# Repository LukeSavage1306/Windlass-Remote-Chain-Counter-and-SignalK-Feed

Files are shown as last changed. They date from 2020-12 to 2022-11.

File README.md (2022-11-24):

# Windlass Remote Control with Chain Counter and Signalk Feed

NOTE: As at mid November 2022 the code, pcb link, images etc are the latest version as described below, but I have yet to update the purchasing links  Should be done in next week or so.

Credit for the original version of this app goes to AK-Hombergers.

The current version:

* Is based on a Wemos D1 Mini (ESP8266) reading pulses from a conventional windlass chain sensor with WiFi access to effect control either directly in AP mode or via the boats main wifi in station mode.
* In AP mode uses mDNS for easy access via a named URL rather than remembering IP addresses
* Provides a wireless remote windlass control from any phone/tablet with wifi capability giving up/down/stop/chain-length-counter/counter-reset functionality and the ability to enter a preset scope to which the windlass will automatically raise/lower the chain.
* Provides chain-length to SignalK via a UDP connection
* Works with 12 volt systems - just requires a single transient suppressor diode to be changed for 24v 
* Will also track chain-length when the windlass is operated by existing controls or when allowed to "free fall"
* LED ON indicates that the board should be operating the windlass.  Off indicates board is in standby
* Stores current chain length in nonvolatile memory so that length is stored on switch off and restored after powering back up.
* Demo mode to check correct operation without need for a gypsy sensor present.
* Detects windlass operation from other existing controls and counts chain for up/down/free fall 

Includes various safety features:

- Safety interlock so that Up/Down will not work if another (existing) control is already operating the windlass.
- Safety stop to stop "anchor up" a preset number of gypsy revolutions before reaching zero (can be changed in code with SAFETY_STOP).
- Safety stop if maximum chain length is reached (can be changed with MAX_CHAIN_LENGTH)
- Safety watchdog timer to stop power after predetermined period of inactivity of client (e.g. due to loss of wifi connection).
- Safety watchdog timer to detect blocked chain. Windlass stops if no events are detected within predetermined period of activity after up/down command.

To implement you need to
* Build and install the windlass control board - PCB design available from the link below
* Configure the code (in Arduino)
   - WLAN type setting WiFiMode_AP_STA to "0" (stand alone access point) or "1" (Client with DHCP for SignalK feed).  Note code assumes SignalK server is at 10.10.10.1.  Configure to suit your set up.  More detail on this below.
   - Configure your wifi SSID and password
   - Calibrate for your sensor (e.g. 0.35 meter per revolution of the gypsy) and the maximum chain length
   - Flash the code to the ESP8266

If working as a standalone Access Point, connect the phone/tablet to the defined network (default SSID is "windlass", password "windlass" - can be changed at lines 23 and 24)  and browse to "windlass.local"  (can be changed at line 195)
If working as WLAN client, browsing to "windlass.local" should still work - although I haven't tested it.  If not determine the DHCP IP address using the Arduino Serial Monitor (or other IDE) and start your browser with that IP address.

This should give you a screen as per below on your phone/tablet.  A flashing red dot in the title bar indicates connection established with the Wemos.

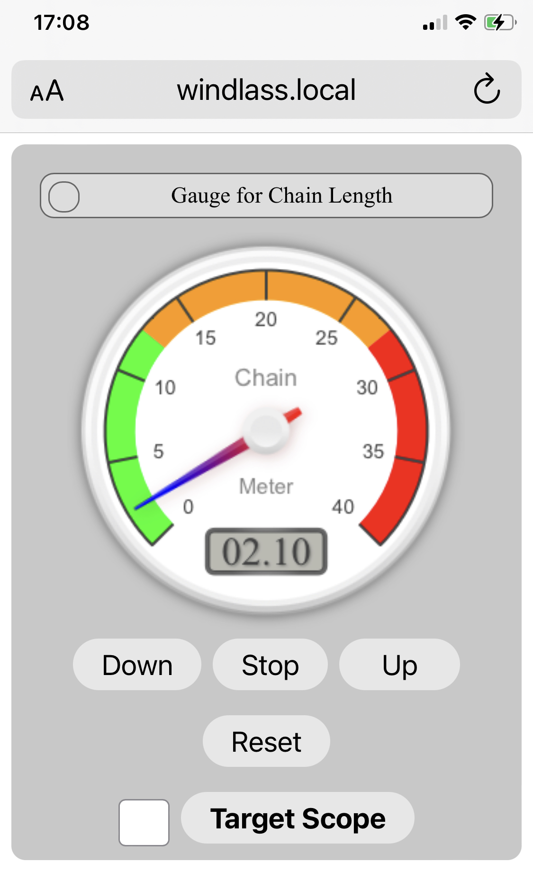
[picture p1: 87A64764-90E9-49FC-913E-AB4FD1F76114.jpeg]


To control the anchor chain relay just press:
- "Down" for anchor down
- "Up" for anchor up
- "Stop" for Stop
- "Reset" to reset the chain counter to zero
- Or enter the desired scope and hit "Target Scope" to pay out/pull in to the set length

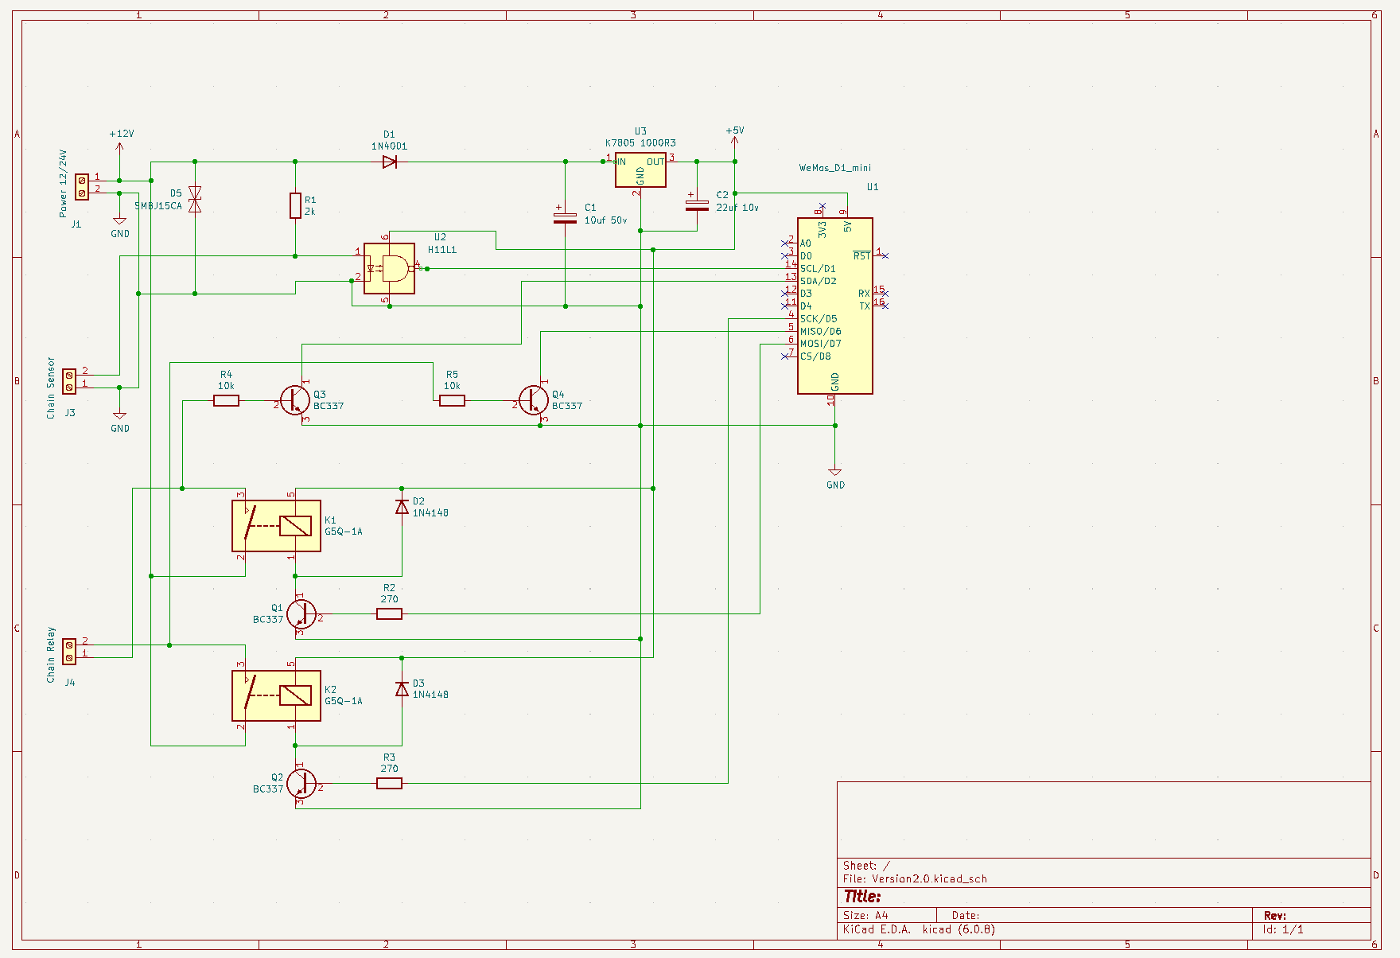
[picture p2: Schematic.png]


A [pcb layout](https://github.com/LukeSavage1306/Windlass-Remote-Chain-Counter-and-SignalK-Feed/blob/main/24vD1MiniWindlassControlAndChainCounter.kicad_pcb) is available in the main folder. 

You can order a PCB from Aisler.net:  https://aisler.net/p/LRMWVSQR

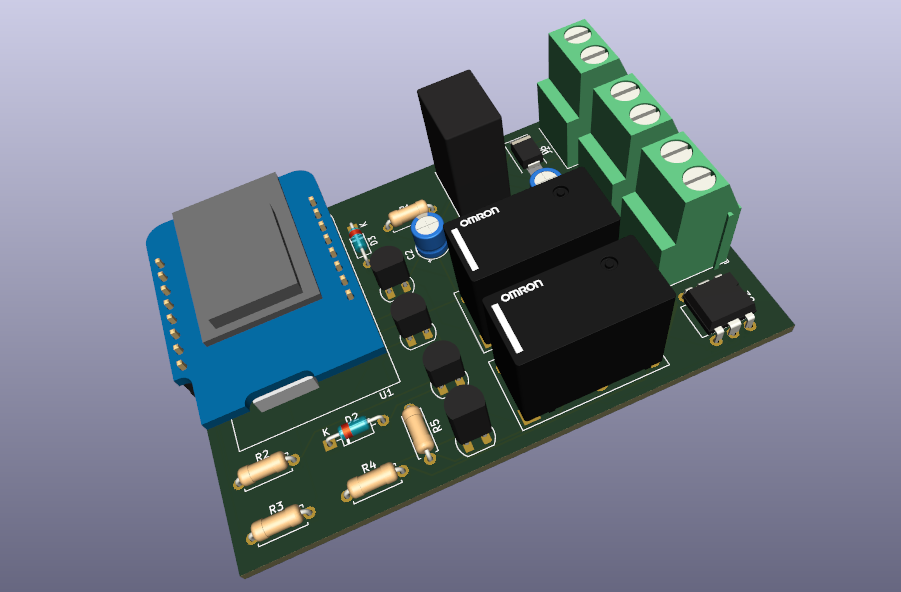
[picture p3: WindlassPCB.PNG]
Board


## Parts:

Parts list currently points to largely German suppliers but are generally widely available with the exception of the PCB. If you want to source these elsewhere I can provide the detailed KiCad files. 

- Board [Link](https://aisler.net/p/ESKPZAUS)
- U1 D1 Mini [Link](https://www.reichelt.de/de/en/d1-mini-esp8266-v3-0-d1-mini-p253978.html?&nbc=1)
- U3 K7805 1000R3L [Link](https://uk.rs-online.com/web/p/switching-regulators/1934015/)
- C1 10uF 50v can electrolytic (can be reduced to 25v if running on a 12V system)
- C2 22uF 15v can electrolytic 
- R1 Resistor 5 KOhm (if using 12v you can reduce this to 2.2 Kohm to ensure accurate counting at low battery voltage) [Link](https://www.reichelt.de/de/en/carbon-film-resistor-1-4-w-5-1-0-kilo-ohms-1-4w-1-0k-p1315.html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)
- R2, R3 Resistor 270 Ohm (*2) [Link](https://www.reichelt.de/de/en/carbon-film-resistor-1-4-w-5-270-ohm-1-4w-270-p1390.html?&nbc=1)
- R4, R5 Resistor 10 KOhm (*2) [Link](https://www.reichelt.de/de/en/carbon-film-resistor-1-4w-5-10-kilo-ohms-1-4w-10k-p1338.html?&nbc=1)
- Q1, Q2, Q3, Q4 Transistor BC337 (*4) [Link](https://www.reichelt.de/de/en/transistor-to-92-bl-npn-45v-800ma-bc-337-25-dio-p219125.html?&nbc=1)
- D2, D3 Diode 1N4148 (*2) [Link](https://www.reichelt.de/schalt-diode-100-v-150-ma-do-35-1n-4148-p1730.html?search=1n4148)
- D1 Diode 1N4001 [Link](https://www.reichelt.de/de/en/rectifier-diode-do41-50-v-1-a-1n-4001-p1723.html?&nbc=1)
- U2 H11-L1 [Link](https://www.reichelt.de/optokoppler-1-mbit-s-dil-6-h11l1m-p219351.html?search=H11-l1)
- K1, K2 Relay (*2) [Link](https://www.reichelt.de/de/en/miniature-power-relay-g5q-1-no-5-v-dc-5-a-g5q-1a-eu-5dc-p258331.html?&nbc=1)
- J1, J3, J4 Connector 2-pin (*3) [Link](https://www.reichelt.de/de/en/2-pin-terminal-strip-spacing-5-08-akl-101-02-p36605.html?&nbc=1)

The current design should work for a Quick or Lofrans anchor chain relay and chain sensor (which looks like a simple reed relay triggerd from a magnet). Connection details  for a Quick windlass/counter can be found here: https://www.quickitaly.com/resources/downloads_qne-prod/1/CHC1203_IT-EN-FR_REV001A.pdf

The board requires connection to your windlass power supply (12v - for 24v change the transient suppressor diode D4 for circa 29v equivalent - no other configuration necessary), connection to your windlass sensor (polarity of connection does not matter) and connection of the Up and Down relay feeds to the existing Up and Down terminals on the main windlass relay (note: the switching terminals that connect to any existing switch controls - NOT the motor output terminals).

To access via the main boat wifi or to send data to SignalK you need to set up in Station mode.  To do that set WiFIMode_AP_STA to 1 at line 21 and define the main boat wifi SSID and Password at lines 23 and 24.   Define the signalk server IP and port at lines 25 and 26.  In Signalk you muse also define a UDP connection.  Go to Server, Connections and define a new connection as per the picture below.  Match the port number to the number you used in the .ino code (default is 4210).  Once configured ChainLength should appear as a data item within the Data Browser.

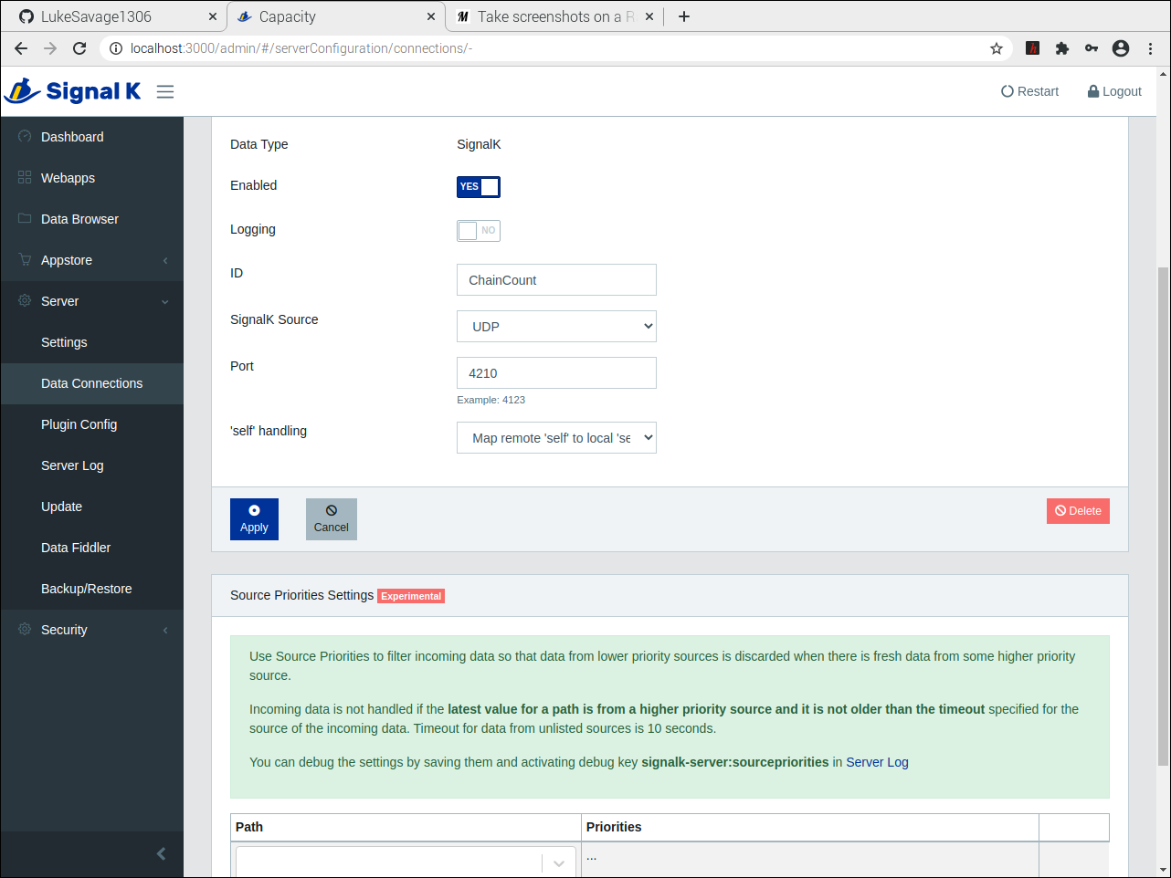
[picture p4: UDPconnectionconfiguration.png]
UDP connection


The gauge display can be changed to mirror your particular chain length in index_html.h   The range is set at lines 133/134 and the coloured zones at line 144

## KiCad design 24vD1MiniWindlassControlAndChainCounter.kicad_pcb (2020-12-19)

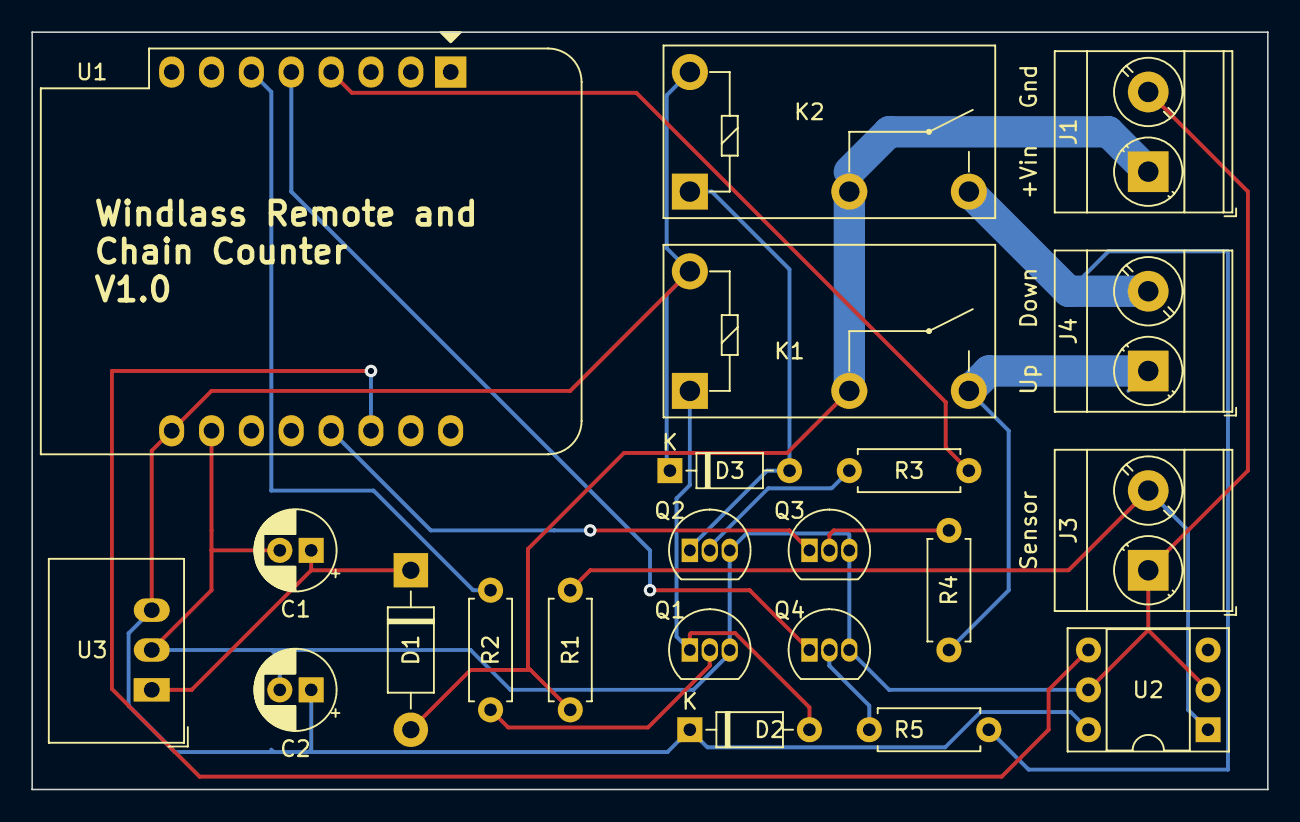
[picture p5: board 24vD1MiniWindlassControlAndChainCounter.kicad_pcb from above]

Board: 2 copper layers, 78.7 x 48.3 mm, 22 parts (0 on the bottom side), 18 nets.

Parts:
C1: 10uF 50V; CP_Radial_D5.0mm_P2.00mm
C2: 22uF10V; CP_Radial_D5.0mm_P2.00mm
D1: 1N4001; D_DO-41_SOD81_P10.16mm_Horizontal
D2, D3: 1N4148; D_DO-35_SOD27_P7.62mm_Horizontal
J1: Power 12/24V; TerminalBlock_Phoenix_MKDS-3-2-5.08_1x02_P5.08mm_Horizontal
J3: Chain Sensor; TerminalBlock_Phoenix_MKDS-3-2-5.08_1x02_P5.08mm_Horizontal
J4: Chain Relay; TerminalBlock_Phoenix_MKDS-3-2-5.08_1x02_P5.08mm_Horizontal
K1, K2: G5Q-1A; Relay_SPST_Omron-G5Q-1A
Q1, Q2, Q3, Q4: BC337; TO-92_Inline
R1: 5k; R_Axial_DIN0207_L6.3mm_D2.5mm_P7.62mm_Horizontal
R2, R3: 270; R_Axial_DIN0207_L6.3mm_D2.5mm_P7.62mm_Horizontal
R4, R5: 10k; R_Axial_DIN0207_L6.3mm_D2.5mm_P7.62mm_Horizontal
U1: WeMos_D1_mini; WEMOS_D1_mini_light
U2: H11L1; DIP-6_W7.62mm_Socket
U3: K7805 1000R3L; Converter_DCDC_RECOM_R-78E-0.5_THT

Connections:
+5V: C2.1, D2.1, D3.1, K1.5, K2.5, U1.9, U2.6, U3.3
+12V: D1.2, J1.1, K1.2, K2.2, R1.1
GND: C1.2, C2.2, J1.2, J3.1, Q1.3, Q2.3, Q3.3, Q4.3, U1.10, U2.2, U2.5, U3.2
unnamed: C1.1, D1.1, U3.1
unnamed: D2.2, K1.1, Q1.1
unnamed: D3.2, K2.1, Q2.1
unnamed: J3.2, R1.2, U2.1
unnamed: J4.1, K1.3, R4.2
unnamed: J4.2, K2.3, R5.2
unnamed: Q1.2, R2.2
unnamed: Q2.2, R3.2
unnamed: Q3.1, U1.13
unnamed: Q3.2, R4.1
unnamed: Q4.1, U1.5
unnamed: Q4.2, R5.1
unnamed: R2.1, U1.6
unnamed: R3.1, U1.4
unnamed: U1.14, U2.4

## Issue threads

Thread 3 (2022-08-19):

Cannot connect to SignalK

MrTom1, 2022-08-19:
I followed exactly your settings to connect to SignalK, however I can not establish any connection. Port settings are same on both sides.
Any advice how to move ahead?

LukeSavage1306, 2022-08-23:
Hi Tom, sorry for slow response.  Have you tried configuring the counter for stand alone use, and then tried connecting directly to its WiFi from your phone?  That way you can make sure that the chip is good and the code is running properly to begin with.   You would then know it is the signalk connection that is playing up rather than a duff chip or bad copy of the code.    Let me know how you get on and we can then work out the next step.

MrTom1, 2022-08-23:
Hi Luke,
Thanks for your reply.
The board is working fine, I can connect to my smartphone and control it from there.
In SignalK I have added the corresponding UDP connection, but no data transfer to there.

LukeSavage1306, 2022-08-23:
So what are the settings you have in the chain counter for connecting to your signal K server?  Do you want to copy and paste those few lines of code?   By the way - I have never done this sort of thing before or since taking Homberger’s counter and making the changes.  I learnt as I went along - largely by trial and error - and that was 2 1/2 years ago.  I only mention that as any help I can give now will also be largely by trial and error!!

MrTom1, 2022-08-23:
So let's try it!
IP address for UDP to SignalK has been adapted (port is 4210, also setup in SignalK according to your manual):
IPAddress ip1(10, 81, 254, 242);           // IP Address to be used for SiganlK so that udp knows where to send messages - amend if yours is different
MMSI adapted:
  char udpmessage[1024];    //Next few lines send metadata to SignalK for chainlength - replace mmsi with your own "self" vessel details
      sprintf(udpmessage, "{\"context\": \"vessels.urn: mrn: imo: mmsi:211695590\",\"updates\": [{\"meta\":[{\"path\": \"navigation.anchor.chainlength\",\"value\": {\"units\": \"m\",\"description\": \"deployed chain length\",\"displayName\": \"Chain Length\",\"shortName\": \"DCL\"}}]}]}");

LukeSavage1306, 2022-08-23:
And line 34 (which you would set to 0 to connect direct) has been reset to 1?

What are you running signalK on?  I used a Raspberry Pi where the default IP for a local host was 10.10.10.1 and that worked fine. I wonder whether in configuring your signalk server as well as changing the IP something else has been changed.

LukeSavage1306, 2022-08-23:
Just re-reading my notes, once connected via the main WiFi (rather than using it standalone) can you access the chain counter from you phone?  But just can’t see the data in signalK?   Or can you not access it from your phone when using it as a client to the main WiFi?

MrTom1, 2022-08-23:
#define WiFiMode_AP_STA 1
IPAddress ip1(10, 81, 254, 242);           // IP Address to be used for SiganlK so that udp knows where to send messages - amend if yours is different

ip1 is the address of the ESP8266 board. This address I also use to run it from my smartphone. Does this address has to be changed?
I changed ip1 to 10.10.10.1 (running on Raspberry Pi) and get the following with the monitor:
WiFi connected
IP address:
10.81.254.242
Now listening at IP 10.81.254.242, UDP port 4210
Metadata sent to SignalKHTTP Server started
{"updates":[{"$source":"Windlass.Control","values":[{"path":"navigation.anchor.chainlength","value":1.650000}]}]}

MrTom1, 2022-08-23:
See above, but still no data for "navigation.anchor.chainlength"

LukeSavage1306, 2022-08-23:
From memory (as I did all of this on another computer at a different location)

The ESP connects to the general boat WiFi router and is allocated an IP address by DHCP.   Your phone, connected to the boat’s WiFi router, then connects to the ESP at the IP allocated via the boat’s router.  It sounds from what you are saying as if that bit is working OK??
Once you are happy that the ESP is accessible via the boat’s WiFi, so we know that it is hooked in, the next thing is then how to get the UDP messages into SignalK.  For that the ESP has to send the messages to the SignalK server running as “local host”.  I think, but can’t remember for sure, that is at 10.10.10.1
I’m afraid I am not going to be back at the location I did this at for a few weeks - and even then I would have to “start again” as, off the top of my head, I can’t even remember how one programmes the ESP from Arduino!!!

LukeSavage1306, 2022-08-23:
Just looking at the code - line 38 is definitely telling the ESP the IP address of SignalK.  So it should be whatever IP your SignalK server is running at, not the IP of the ESP.  Something also makes me think that it sends data when there is an update to the value, not on a regular basis, so if you are not winding up or down it won’t be sending anything.  Not sure my knowledge of the coding is good enough to confirm that from “reading” it rather than trying it!

To help get it working (which took me days of trial and error) I wired up a simple switch to simulate the windlass switch - and I think changed the timeout time so that I could do it slowly

MrTom1, 2022-08-23:
Got it running!
ip1 set to the correct address of the Raspi SignalK Server (10.81.254. ...) and it works fine!

Thanks for your time and advices!
Tom

LukeSavage1306, 2022-08-23:
At line 166 it seems you should see a line on the monitor if the metadata has been correctly sent.  Are you seeing that?

LukeSavage1306, 2022-08-23:
Brilliant.  One thing to check when you install it.  Depending on the rating of your windlass power relay the current draw to operate the relay could be quite high.  Part of the redesign of the circuit board from Homberger’s original design was to upgrade the size of, and shorten the PCB tracks between the onboard relay and the connector.  On mine it seems OK - but you may want to check that the board isn’t getting hot in that area.

Good luck - I hope it makes your anchoring easier.  Where are you based by the way??

Luke

On 23 Aug 2022, at 15:25, MrTom1 ***@***.***> wrote:

Got it running!
ip1 set to the correct address of the Raspi SignalK Server (10.81.254. ...) and it works fine!

Thanks for your time and advices!
Tom

—
Reply to this email directly, view it on GitHub, or unsubscribe.
You are receiving this because you commented.

MrTom1, 2022-08-23:
Good advice to check the current and signal line.

I'm based at Lake of Constance, Germany
Another happy user of the anchoring tool there now ;-)

LukeSavage1306, 2022-08-23:
Great.  If you have any ideas on improvements let me know.  In the meantime I’m going to close the thread.
Regards
Luke

Closed 2022-08-23.

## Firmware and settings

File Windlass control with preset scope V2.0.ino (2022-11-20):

// Anchor Chain Remote Control / Chain Counter with WLAN.
// and Preset Target Scope
// SignalK feed, external control, freefall, LED status
// Version 2.0  07/11/2022

#include<ESP8266WiFi.h>
#include<ESP8266WebServer.h>
#include<EEPROM.h>
#include <WiFiUdp.h>
#include <ESP8266mDNS.h>              // Used to enable web browser to find by URL rather than IP address


#include "index_html.h"              // Webserver script for Gauge/Buttons on phone/tablet

#define ENABLE_DEMO 1                // Set to 1 to enable Demo Mode with up/down counter
#define SAFETY_STOP 2                // Defines safety stop for chain up. Stops defined number of revolutions before reaching zero
#define MAX_CHAIN_LENGTH 39          // Define maximum chain lengthin metres. Relay turns off after the value is reached

// Wifi: Select AP or Client

#define WiFiMode_AP_STA 0             // Defines WiFi Mode 0 -> AP (with IP:192.168.4.1 stand alone and  1 -> Station (client with IP: via DHCP)
                                        // To use both the windlass control and feed SignalK you have to set to 1 as a Station 
const char *ssid = "Windlass";          // Set WLAN name for station connection
const char *password = "Windlass";  // Set password for station connection
IPAddress ip1(10, 10, 10, 1);           // IP Address to be used for SiganlK so that udp knows where to send messages - amend if yours is different
unsigned int outPort = 4210;            // and which port to send to


ESP8266WebServer server(80);                //Define Web Server at port 80 for general connection to central boat wifi


// Chain Counter
 
#define Chain_Calibration_Value 0.35 // Translates counter pulses to metres per revolution - change this to suit your windlass
#define Chain_Counter_Pin D1         // Counter impulse is measured as interrupt on pin D1, GPIO pin 05
unsigned long Last_int_time = 0;     // Time of last interrupt
unsigned long Last_event_time = 0;   // Time of last event for engine watchdog
unsigned long Last_stop_time = 0;    // Time of stop request - used to continue correct counting while windlass slows to a halt
unsigned long Sprint_timer = 0;       // Timer to control serial monitor printing
int ChainCounter = 0;                // Counter for chain events
int Scope = 0;                        // Preset Target Scope
int LastSavedCounter = 0;            // Stores last ChainCounter value to allow storage to nonvolatile storage in case of value changes

// Relay

#define Chain_Up_Pin D7              // GPIO pin 13 for Chain Up Relay       (If using a board other than Wemos D1 mini then check all pins)
#define Chain_Down_Pin D5            // GPIO pin 14 for Chain Down Relay      
#define Chain_Up_Override_Pin D2     // GPIO pin 04 for Chain Up Override     
#define Chain_Down_Override_Pin D6   // GPIO pin 12 for Chain Down Override   
int UpDown = 1;                      // 1 =  Chain down / count up, -1 = Chain up / count backwards
int OnOff = 0;                       // Relay On/Off - Off = 0, On = 1
int Preset = 0;                      // Flag to control logic in reaching preset scope
unsigned long Watchdog_Timer = 0;    // Watchdog timer to stop relay after 1 second of inactivity e.g. connection loss to client


// Chain Event Interrupt
// Enters on falling edge

void IRAM_ATTR handleInterrupt() {    //This section debounces the chain sensor to avoid multipe counts from one switch event
  noInterrupts();

  if (millis() > Last_int_time + 100) {  // Debouncing. No new events for 100 milliseconds - still a fraction of a turn of the windlass

    ChainCounter += UpDown;             //Increment/decrement chain counter based on sign of UpDown

  //This section handles testing against reaching a preset value

    if ((Preset == 1) && (UpDown == 1) && (Scope-(ChainCounter*Chain_Calibration_Value) <= 0 )) {       //Test to see if chain let out to preset scope - and if so....
    OnOff = 0;                                                                                        //Set status to off
    Last_stop_time = millis();                                                                        //Record time (used to allow for deceleration interval of windlass)      
    Preset = 0;                                                                                       //Flag end of preset operation
    digitalWrite(Chain_Up_Pin, LOW );                                                                 //Make sure both relays are off  
    digitalWrite(Chain_Down_Pin, LOW);
  }

  if ((Preset == 1) && (UpDown == -1) && ((ChainCounter*Chain_Calibration_Value)-Scope <= 0 )) {      //Test to see if chain is taken in to preset scope - and if so.....
    OnOff = 0;                                                                                        //Set status to off
    Last_stop_time = millis();                                                                        //Record time (used to allow for deceleration interval of windlass)
    Preset = 0;                                                                                       //Flag end of preset operation
    digitalWrite(Chain_Up_Pin, LOW );                                                                 //Make sure both relays are off
    digitalWrite(Chain_Down_Pin, LOW);
  }

   //This section handles reaching the upper safety stop limit     

  if ( ( (ChainCounter <= SAFETY_STOP) && (UpDown == -1) && (OnOff == 1) )) {    // If safety stop counter reached while chain is going up - 
    digitalWrite(Chain_Up_Pin, LOW );                                             // Turn off both relays
    digitalWrite(Chain_Down_Pin, LOW );
    OnOff = 0;                                                                    // Set the status to off
    Last_stop_time = millis();
    Serial.print("Up safety stop reached - Turning off Up relay and UpDown state is ");
    Serial.println(UpDown);
    }
  
  
  
  if  ( (UpDown == 1) && (abs(ChainCounter) * Chain_Calibration_Value >= MAX_CHAIN_LENGTH) )  {  // Maximum chain length reached - so turn off

    digitalWrite(Chain_Up_Pin, LOW );
    digitalWrite(Chain_Down_Pin, LOW );
    OnOff = 0;
    Serial.print("Maximum chain length reached - Turning off Down relay and UpDown state is ");
    Serial.println(UpDown);

    } 
    Last_event_time = millis();         // Store last event time to detect blocking chain
    }

  
  Last_int_time = millis();             // Store last interrupt time for debouncing
  interrupts();
}

 WiFiUDP Udp;                         // Configure UDP - not sure if these lines are necessary as we are transmitting rather than receiving via UDP
unsigned int localUdpPort = 4210;  // local port to listen on
char incomingPacket[255];  // buffer for incoming packets
char  replyPacket[] = "Hi there! Got the message :-)";  // a reply string to send back


void setup() {
  
  // LED indicator
  pinMode(LED_BUILTIN,OUTPUT); //Define LED pin as output
  digitalWrite(LED_BUILTIN,HIGH); //and turn it off
  
  int wifi_retry = 0;

  // Relay output
  pinMode(Chain_Up_Pin, OUTPUT);            // Sets pin as output
  pinMode(Chain_Down_Pin, OUTPUT);          // Sets pin as output
  digitalWrite(Chain_Up_Pin, LOW );         // and relay off
  digitalWrite(Chain_Down_Pin, LOW );       // and relay off
  
  //Over Ride input
  pinMode(Chain_Down_Override_Pin, INPUT_PULLUP);  // Sets pin as input pulled high 
  pinMode(Chain_Up_Override_Pin, INPUT_PULLUP);    // Sets pin as input pulled high

  // Init Chain Count measure with interrupt
  pinMode(Chain_Counter_Pin, INPUT_PULLUP); // Sets pin as input pulled high
  attachInterrupt(digitalPinToInterrupt(Chain_Counter_Pin), handleInterrupt, FALLING); // Attaches pin to interrupt on falling edge

  // Init serial monitor for debugging
  Serial.begin(38400);
  Serial.print("");
  Serial.println("Start");

  EEPROM.begin(16);
  ChainCounter = EEPROM.read(0);
  LastSavedCounter = ChainCounter;                  // Initialise last counter value so that after power off it restarts with the same length

  // Init WLAN AP
  if (WiFiMode_AP_STA == 0) {

    WiFi.mode(WIFI_AP);                              // WiFi Mode Access Point
    delay (100);
    WiFi.softAP(ssid, password); // AP name and password
    Serial.println("Start WLAN AP");
    Serial.print("IP address: ");
    Serial.println(WiFi.softAPIP());



  } else {

    Serial.println("Start WLAN Client DHCP");         // WiFi Mode Client with DHCP
    WiFi.begin(ssid, password);

    while (WiFi.status() != WL_CONNECTED) {           // Check connection
      wifi_retry++;
      delay(500);
      Serial.print(".");
      if (wifi_retry > 10) {
        Serial.println("\nReboot");                   // Reboot after 10 connection tries
        ESP.restart();
      }
    }
  Serial.println("");
  Serial.println("WiFi connected");
  Serial.println("IP address: ");
  Serial.println(WiFi.localIP());
  
  Udp.begin(localUdpPort);
  
  Serial.printf("Now listening at IP %s, UDP port %d\n", WiFi.localIP().toString().c_str(), localUdpPort);
  
      char udpmessage[1024];    //Next few lines send metadata to SignalK for chainlength - replace mmsi with your own "self" vessel details
      sprintf(udpmessage, "{\"context\": \"vessels.urn: mrn: imo: mmsi: 235083375\",\"updates\": [{\"meta\":[{\"path\": \"navigation.anchor.chainlength\",\"value\": {\"units\": \"m\",\"description\": \"deployed chain length\",\"displayName\": \"Chain Length\",\"shortName\": \"DCL\"}}]}]}");
      Udp.beginPacket(ip1, outPort);
      Udp.write(udpmessage);
      Udp.endPacket();
      Serial.printf("Metadata sent to SignalK");
      
}

if (!MDNS.begin("windlass")) {                                                // Start the mDNS responder for windlass.local
    Serial.println("Error setting up MDNS responder!");
  }
  Serial.println("mDNS responder started");


// Handle HTTP request events from phone/tablet

server.on("/", Event_Index);
server.on("/gauge.min.js", Event_js);
server.on("/ADC.txt", Event_ChainCount);
server.on("/up", Event_Up);
server.on("/down", Event_Down);
server.on("/stop", Event_Stop);
server.on("/reset", Event_Reset);
server.on("/preset", Event_Preset);
server.onNotFound(handleNotFound);

server.begin();
Serial.println("HTTP Server started");
}

//HANDLE UP REQUEST
void Event_Up() {    
  if (((OnOff == 0 && digitalRead(Chain_Up_Override_Pin) == HIGH && digitalRead(Chain_Down_Override_Pin) == HIGH)) || (OnOff == 1)) { // Execute only if the app is already on, or if there isn't a manual override present
    server.send(200, "text/plain", "-1000");                                                                                          // Send response "-1000" means no  chainlength
     UpDown = -1;																													// Set chain counter to reduce scope
    Serial.println("Up button pressed - setting UpDown to -1 and Turning on Up relay by setting Chain_Up_Pin to High");				//Debug message
      digitalWrite(Chain_Down_Pin, LOW );                                                                                             //  Make sure down relay is off
      digitalWrite(Chain_Up_Pin, HIGH ); 																							//Then turn up relay on																						
      OnOff = 1;																													//With app on
      Preset = 0;																													//And target preset scope off
       Last_event_time = millis();                                        //Record event time for checking if windlass is jammed
  }
}
//HANDLE DOWN REQUEST
void Event_Down() {  
  if (((OnOff == 0 && digitalRead(Chain_Up_Override_Pin) == HIGH && digitalRead(Chain_Down_Override_Pin) == HIGH)) || (OnOff == 1)) { // Execute only if the app is already on, or if there isn't a manual override present
    server.send(200, "text/plain", "-1000");  // Send response "-1000" means no  chainlength
    UpDown = 1;                                                                                                                       // Set chain counter to increase scope
    Serial.println("Down button pressed - setting UpDown to 1 and Turning on Down relay by setting Chain_Down_Pin to High");          // Debug message
    digitalWrite(Chain_Up_Pin, LOW );                                                                                                 // Make sure up relay is off
    digitalWrite(Chain_Down_Pin, HIGH );                                                                                              // And turn down relay on
    Last_event_time = millis();                                                                                                       // Record event time for checking if windlass is jammed
    OnOff = 1;                                                                                                                        // With app on
    Preset = 0;                                                                                                                       // and preset off 
  Last_stop_time = millis();                                                                                                          // Record event time for checking if windlass is jammed
  }
}
//HANDLE STOP REQUEST
void Event_Stop() {  
  server.send(200, "text/plain", "-1000");  // Send response "-1000" means no  chainlength
  Serial.print("Stop button pressed - setting both Chain Pins to Low, current UpDown state is ");                                     // Debug message
  Serial.println(UpDown);                                                                                                             // Debug message    
  Last_stop_time = millis();
  digitalWrite(Chain_Up_Pin, LOW );                                                       // Make sure both relays are off
  digitalWrite(Chain_Down_Pin, LOW );
  OnOff = 0;                                                                              // With app off
  Preset = 0;                                                                             // And Preset off
}


//HANDLE REQUEST TO RESET COUNTER TO ZERO
void Event_Reset() {        
    ChainCounter = 0;                                             //Reset counter to zero
  server.send(200, "text/plain", "-1000");  // Send response "-1000" means no  chainlength
  Serial.println("Reset gauge to zero");                          //Debug message
}


//HANDLE PRESET SCOPE LENGTH REQUEST
void Event_Preset() {               
  server.send(200, "text/html", indexHTML);                                                                                           // Refresh browser page (ideally don't but can't work out how not to)
  Scope = (server.arg(0)).toInt();                                                                                                    // Take preset scope from input and convert it to an integer     

  Serial.print("Scope has been set to ");                                                                                             // Send length to serial print for debugging
  Serial.println(Scope);

  Preset = 1;                                                                                                                         // Set Flag for preset scope logic
  if (Scope - (ChainCounter*Chain_Calibration_Value) > 0) {                                                                           // Determine if chain needs to go out to reach preset scope
  Serial.println ("Chain needs to go out by ");                                                                                       // Debug message 
  Serial.println (Scope - (ChainCounter*Chain_Calibration_Value));                                                                    // Debug message
  UpDown =1;                                                                                                                          // Set counter for down                                 
  digitalWrite(Chain_Up_Pin, LOW);                                                                                                    //Make sure up relay is off and 
  digitalWrite(Chain_Down_Pin, HIGH);                                                                                                // Turn on down relay
  OnOff = 1;                                                                                                                        // And flag that app is on

  } else {                                                                                                                             //Chain needs to come up to reach preset scope
  Serial.println ("Chain needs to go up by ");
  Serial.println ((ChainCounter*Chain_Calibration_Value)-Scope);
  UpDown = -1;                                                                                                                        //Set counter for up
  digitalWrite(Chain_Down_Pin, LOW);                                                                                                  //Make sure down relay is off and 
  digitalWrite(Chain_Up_Pin, HIGH);                                                                                                   // Turn on up relay
  OnOff = 1;                                                                                                                          // And flag that app is on
  }
  Last_event_time = millis(); 
  Watchdog_Timer = millis();     
}

void Event_Index() {                         // If "http://<ip address>/" requested
  server.send(200, "text/html", indexHTML);  // Send Index Website
}


void Event_js() {                            // If "http://<ip address>/gauge.min.js" requested
  server.send(200, "text/html", gauge);      // Then send gauge.min.js
}
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
void loop() {
  int wifi_retry = 0;
  MDNS.update();                                                    // Check to see if browser is looking for IP address
  server.handleClient();                                           // Handle HTTP requests

  if ( ( millis() > Watchdog_Timer + 1000 ) ||                     // Check HTTP connnection for activity in last 1 second (>1 second implies Wifi connection lost)
       ( (OnOff == 1) && (millis() > Last_event_time + 1500)) )  { // Check if engine is on but with no in last 1.5 seconds (>1.5 seconds implies windlass is not rotating/jammed)

    digitalWrite(Chain_Up_Pin, LOW );                              // If either show no activity then turn relays off   COMMENT OUT THESE THREE LINES TO BENCH TEST
    digitalWrite(Chain_Down_Pin, LOW );
    OnOff = 0;
    Serial.println("Turning off due to watchdog or event timer");
  }

  if ((OnOff == 1 && (digitalRead(Chain_Up_Override_Pin) == LOW)) || (OnOff == 1 && (digitalRead(Chain_Down_Override_Pin)) == LOW)) { //If the app is on and one of the relays is operated
    digitalWrite(BUILTIN_LED, LOW);                                                     // then turn on the LED
  } else {                                                                              // otherwise
    digitalWrite(BUILTIN_LED, HIGH);                                                    // turn it off
  }

  if (OnOff == 0) {                                     // If App is off  ...
    if (digitalRead(Chain_Up_Override_Pin) == LOW && millis() > Last_stop_time + 2500) {      // and there is a manual chain up over-ride
      UpDown = -1;                                          // set counter to reduce chain count
    } else if ( millis() > Last_stop_time + 2500) {
      UpDown = 1;                                           // otherwise if App is off then set to increase counter ie free fall or powered down..  Timer stops chain pulses as chain up slows to a stop being treated as down.
    }
  }
 if (millis() - Sprint_timer >500) {
Serial.print("Chain count is ");
Serial.print(ChainCounter * Chain_Calibration_Value); 
Serial.print("UpDown = ");
Serial.print(UpDown);
Serial.print(" Up Override = ");
Serial.print(digitalRead(Chain_Up_Override_Pin));
Serial.print(" Down Override = ");
Serial.println(digitalRead(Chain_Down_Override_Pin));
Sprint_timer = millis();
 }
  if (ChainCounter != LastSavedCounter) {                          // If ChainCounter has changed then store new value to nonvolatile storage (if changed)
    EEPROM.write(0, ChainCounter);
    EEPROM.commit();
    LastSavedCounter = ChainCounter;


    float temp = (ChainCounter * Chain_Calibration_Value);            // Caluclate new length to send to SignalK

    char udpmessage[1024];      // This and next few lines send the new length to SignalK.  You can change the  source if you wish.
   sprintf(udpmessage, "{\"updates\":[{\"$source\":\"ESP8266.Windlass.Control\",\"values\":[{\"path\":\"navigation.anchor.chainlength\",\"value\":%f}]}]}", temp);
    Udp.beginPacket(ip1, outPort);
    Udp.write(udpmessage);
    Udp.endPacket();


    // Serial.println(udpmessage); // print udpmessage to serial monitor in Arduino IDE, so can check JSON structure of the message is correct

  }

  if (WiFiMode_AP_STA == 1) {                                      // Check connection if working as client
    while (WiFi.status() != WL_CONNECTED && wifi_retry < 5 ) {     // Connection lost, 5 tries to reconnect
      wifi_retry++;
      Serial.println("WiFi not connected. Try to reconnect");
      WiFi.disconnect();
      WiFi.mode(WIFI_OFF);
      WiFi.mode(WIFI_STA);
      WiFi.begin(ssid, password);
      delay(100);
    }
    if (wifi_retry >= 5) {
      Serial.println("\nReboot");                                  // Did not work -> restart ESP8266
      ESP.restart();
    }





  }



  // Dummy to empty input buffer to avoid board to stuck with e.g. NMEA Reader
  if ( Serial.available() ) {
    Serial.read();
  }
}

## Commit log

2020-12-10 Create ChainCounter
2020-12-12 Update ChainCounter
2020-12-16 Create WIP chaincount
2020-12-16 Update WIP chaincount
2022-11-20 Updated version with new features and improved pcb
    Several enhancements including the ability to pay out or wind in to a pre-set scope, easier access from a browser using mDNS, improved board stability with transient voltage suppression
    [Windlass control with preset scope V2.0.ino]
